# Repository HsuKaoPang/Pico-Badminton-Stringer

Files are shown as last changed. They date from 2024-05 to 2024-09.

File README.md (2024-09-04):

# Pico Stringer
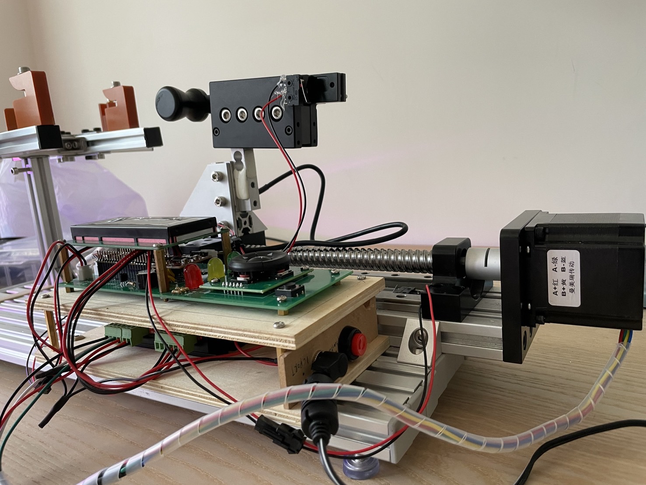
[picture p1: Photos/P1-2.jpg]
images1-1

The project is my version of how to make a badminton stringer, based on [PicoBETH](https://github.com/206cc/PicoBETH) DIY badminton stringer prjoect. 
I published the assemable guildline on [Instructables](https://www.instructables.com/DIY-Electric-Badminton-Stringers/). 

## Modification
Compare to original PicoBETH project, several modifications are listed below. 

### Hardware:
1. Based on a simple badminton stringer, which I bought from [Taobao](https://item.taobao.com/item.htm?_u=t20cga269s9bcb&id=737728917603&spm=a1z09.2.0.0.3fa02e8dvmYHSh). the stringer is made mostly by 2020 and 2060 alumium extrusions.

2. Applying extra 2060 alumium extrusions and alumium extrusion parts as the project's platform.
3. GX-80 1610 double-guided liner guideway with 200mm stroke is adopted.
4. Change Stepper motor driver to DM542C stepper driver.
In my past experience, DM542C could run stepper motor smoother and quieter then TB6600. It also supports more microstep and current adjuestments.

5. Custom-designed PCB board.
6. Intergrated HX711 layout based on [Sparkfun hx711 module](https://www.sparkfun.com/products/13879)

PCB V2.0 Updated:
1. Shrink PCB size to 55.00 x 176.00 mm
2. Extra 12V power pin is preserved for further stepper motor driver development.
3. rearrangement of connector pin.
4. 5-way switch intergrated.
5. polygon poured on both side.

### Software:
[main.py]() is slightly modified to fit DM542C driver.

## Worning

I improved the stringer's strength before I start the project. If your stringer is not robost, I strongly advise against undertaking this project. A weak stringer platform might deform after applying tension, causing the racket frame to deform into round shape or even damage the racket.

## Documents

1. Schmatic diagrams

2. GERBER file
3. BOM of customized pcb board
4. BOM of stringer platfrom hardware
5. Softwares 
## Acknowledgements

 - [PicoBETH](https://github.com/206cc/PicoBETH)
 - [Simple badmintion Stringer](https://item.taobao.com/item.htm?_u=t20cga269s9bcb&id=737728917603&spm=a1z09.2.0.0.3fa02e8dvmYHSh)
 - [Sparkfun HX711](https://www.sparkfun.com/products/13879)
 - [Micropython - hx711-pico-mpy](https://github.com/endail/hx711-pico-mpy)
 - [Micropython - RPI-PICO-I2C-LCD](https://github.com/T-622/RPI-PICO-I2C-LCD)

## Support

For support, feel free to contact me through bill10361239@gmail.com.

## Authors

- [@HsuKaoPang](https://www.github.com/HsuKaoPang)

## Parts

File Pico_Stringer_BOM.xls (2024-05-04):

Comment | Description | Designator | Footprint | LibRef | Quantity
104 | SMD Cap | C1, C3, C5, C6, C8, C10, C11 | 6-0805_M | C | 7
10uF | SMD Cap | C2, C4, C7, C9 | C1210_M | C | 4
IN5819 | Schottky Diode | D1 | DO-41 | D Schottky | 1
LED_G | Typical RED, GREEN, YELLOW, AMBER GaAs LED | D2 | 10mm LED | LED2 | 1
LED_Y | Typical RED, GREEN, YELLOW, AMBER GaAs LED | D3 | 10mm LED | LED2 | 1
LED_R | Typical RED, GREEN, YELLOW, AMBER GaAs LED | D4 | 10mm LED | LED2 | 1
Botton head | 2P Connector | J1 | XH2.54-LI-2P | Header 2 | 1
Front Limit | 2P Connector | J2 | XH2.54-LI-2P | Header 2 | 1
Rear Limit | 2P Connector | J3 | XH2.54-LI-2P | Header 2 | 1
STEPPER | DIR PUL | J4 | XH2.54-LI-4P | Header 4 | 1
Exit Botton | 2P Connector | J5 | 12x12mm SWITCH | Header 2 | 1
5-way switch | 6P Connector | J6 | 5WAY_SWITCH | Header 6 | 1
2004 LCD | 2004 I2C LCD | J7 | HDR1X4 | Header 4 | 1
HX711 | HX711 module | J8 | HX711_MODULE | Header 4 | 1
20KG | Keyes Hx711 module | J9 | HDR1X4 | Header 4 | 1
HDR-1X2 | 5V | JP1 | XH2.54-LI-2P | Header 2 | 1
10uH | SMD Ind | L1 | L 1210 | L | 1
Buzzer | Magnetic Transducer Buzzer | LS1 | Buzzer | Buzzer | 1
SS8050 | NPN | Q1 | TO92A | 8050-DIP | 1
MMBT4403 | PNP | Q2 | SOT23-3L | 8550-SMD | 1
150 | Resistor | R1, R3, R4 | AXIAL-0.3 | Res1 | 3
10K | Resistor | R2 | AXIAL-0.3 | Res1 | 1
1K | Resistor | R5 | AXIAL-0.3 | Res1 | 1
10K | SMD Res | R6 | 6-0805_N | R | 1
20K | SMD Res | R7 | 6-0805_M | R | 1
0K | SMD Res | R8 | 6-0805_M | R | 1
8.2K | SMD Res | R9 | 6-0805_M | R | 1
100 | SMD Res | R10, R11 | 6-0805_M | R | 2
Pi Pico |  | U1 | PICO | Pi Pico | 1
HX711 |  | U2 | SOP16 | HX711 | 1
AMS1117-5.0 | Voltage Regulator | VR1 | AMS1117 | Volt Reg | 1

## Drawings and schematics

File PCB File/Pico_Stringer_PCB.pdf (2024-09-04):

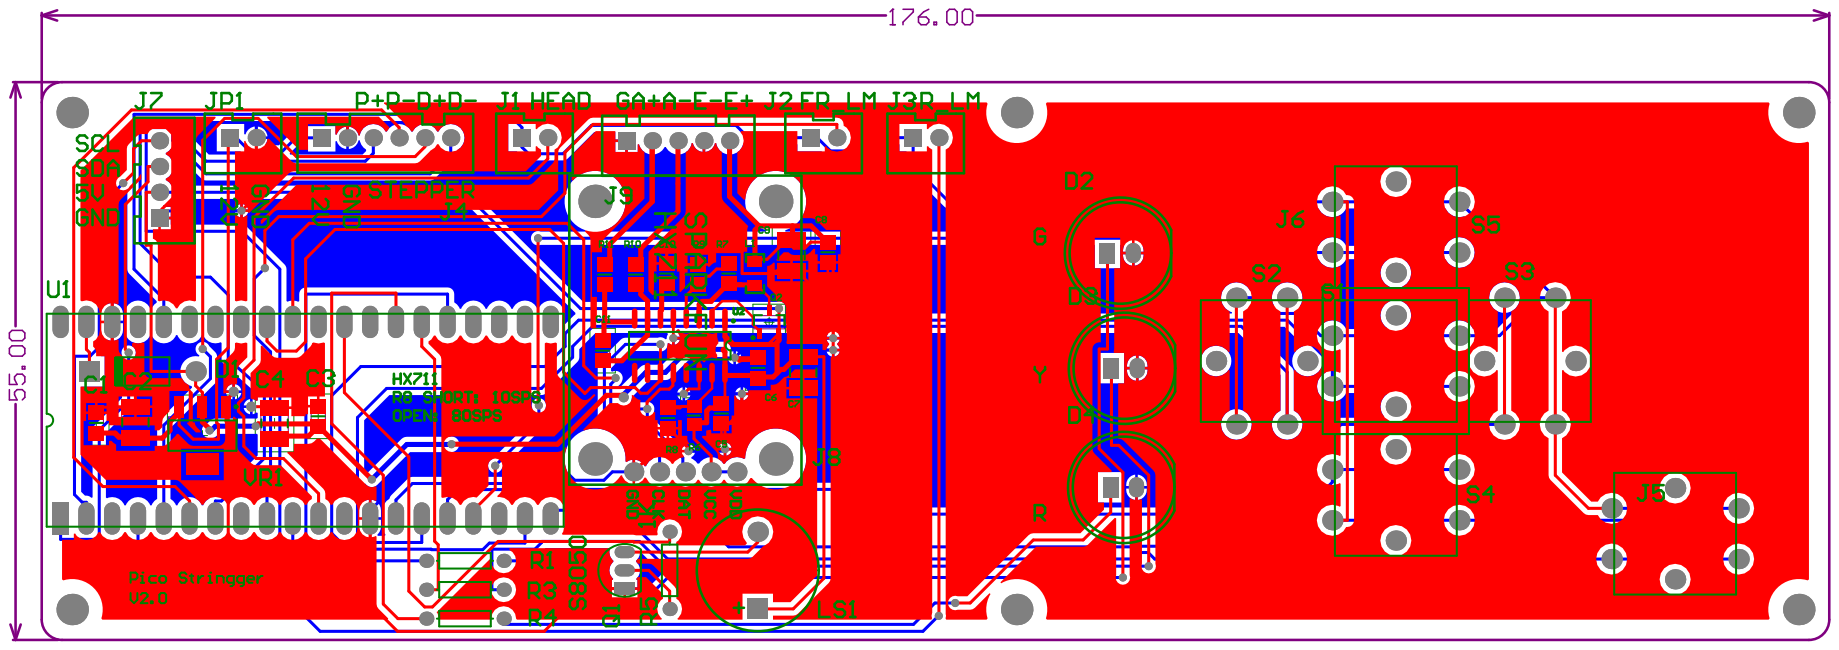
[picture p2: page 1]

Comment | Description | Designator | Footprint | LibRef | Quantity
104 | 贴片电容 | C1 | 6-0805_M | C | 1
10uF | 贴片电容 | C2 | C1210_M | C | 1
104 | 贴片电容 | C3 | 6-0805_M | C | 1
10uF | 贴片电容 | C4 | C1210_M | C | 1
104 | 贴片电容 | C5 | 6-0805_M | C | 1
104 | 贴片电容 | C6 | 6-0805_M | C | 1
10uF | 贴片电容 | C7 | C1210_M | C | 1
104 | 贴片电容 | C8 | 6-0805_M | C | 1
10uF | 贴片电容 | C9 | C1210_M | C | 1
104 | 贴片电容 | C10 | 6-0805_M | C | 1
104 | 贴片电容 | C11 | 6-0805_M | C | 1
IN5819 | Schottky Diode | D1 | DO-41 | D Schottky | 1
LED_G | Typical RED, GREEN, YELLOW, AMBER GaAs LED D2 | | 10mm LED | LED2 | 1
LED_Y | Typical RED, GREEN, YELLOW, AMBER GaAs LED D3 | | 10mm LED | LED2 | 1
LED_R | Typical RED, GREEN, YELLOW, AMBER GaAs LED D4 | | 10mm LED | LED2 | 1
Botton head | 2P接插件 | J1 | XH2.54-LI-2P | Header 2 | 1
Front Limit | 2P接插件 | J2 | XH2.54-LI-2P | Header 2 | 1
Rear Limit | 2P接插件 | J3 | XH2.54-LI-2P | Header 2 | 1
6pin STEPPER | Header, 6-Pin | J4 | XH2.54-LI-6P | Header 6 | 1
Exit Botton | 2P接插件 | J5 | R-Button | Header 2 | 1
5-way switch | | J6 | 5-head button | 5-way switch | 1
2004 LCD | 2004 I2C LCD | J7 | XH2.54-LI-4P | Header 4 | 1
HX711 | SPARKFUN_HX711J8 | | SPARKFUN_HX711Header 5 | | 1
HDR-1X5 | Keyes Hx711 moduleJ9 | | XH2.54-LI-5P | Header 5 | 1
HDR-1X2 | 5V | JP1 | XH2.54-LI-2P | Header 2 | 1
10uH | 小功率贴片电感 | L1 | L 0805 | L | 1
Buzzer | Magnetic Transducer Buzzer LS1 | | Buzzer | Buzzer | 1
SS8050 | 高频放大-NPN型 | Q1 | TO92A | 8050-DIP | 1
MMBT4403 | 高频放大-PNP型 | Q2 | SOT23-3L | 8550-SMD | 1
150 | Resistor | R1 | AXIAL-0.3 | Res1 | 1
150 | Resistor | R3 | AXIAL-0.3 | Res1 | 1
150 | Resistor | R4 | AXIAL-0.3 | Res1 | 1
1K | Resistor | R5 | AXIAL-0.3 | Res1 | 1
10K | 贴片电阻 | R6 | 6-0805_N | R | 1
20K | 贴片电阻 | R7 | 6-0805_M | R | 1
0K | 贴片电阻 | R8 | 6-0805_M | R | 1
8.2K | 贴片电阻 | R9 | 6-0805_M | R | 1
100 | 贴片电阻 | R10 | 6-0805_M | R | 1
100 | 贴片电阻 | R11 | 6-0805_M | R | 1
Pi Pico | | U1 | PICO | Pi Pico | 1
HX711 | | U2 | SOP16 | HX711 | 1
AMS1117-5.0 | Voltage Regulator | VR1 | AMS1117 | Volt Reg | 1

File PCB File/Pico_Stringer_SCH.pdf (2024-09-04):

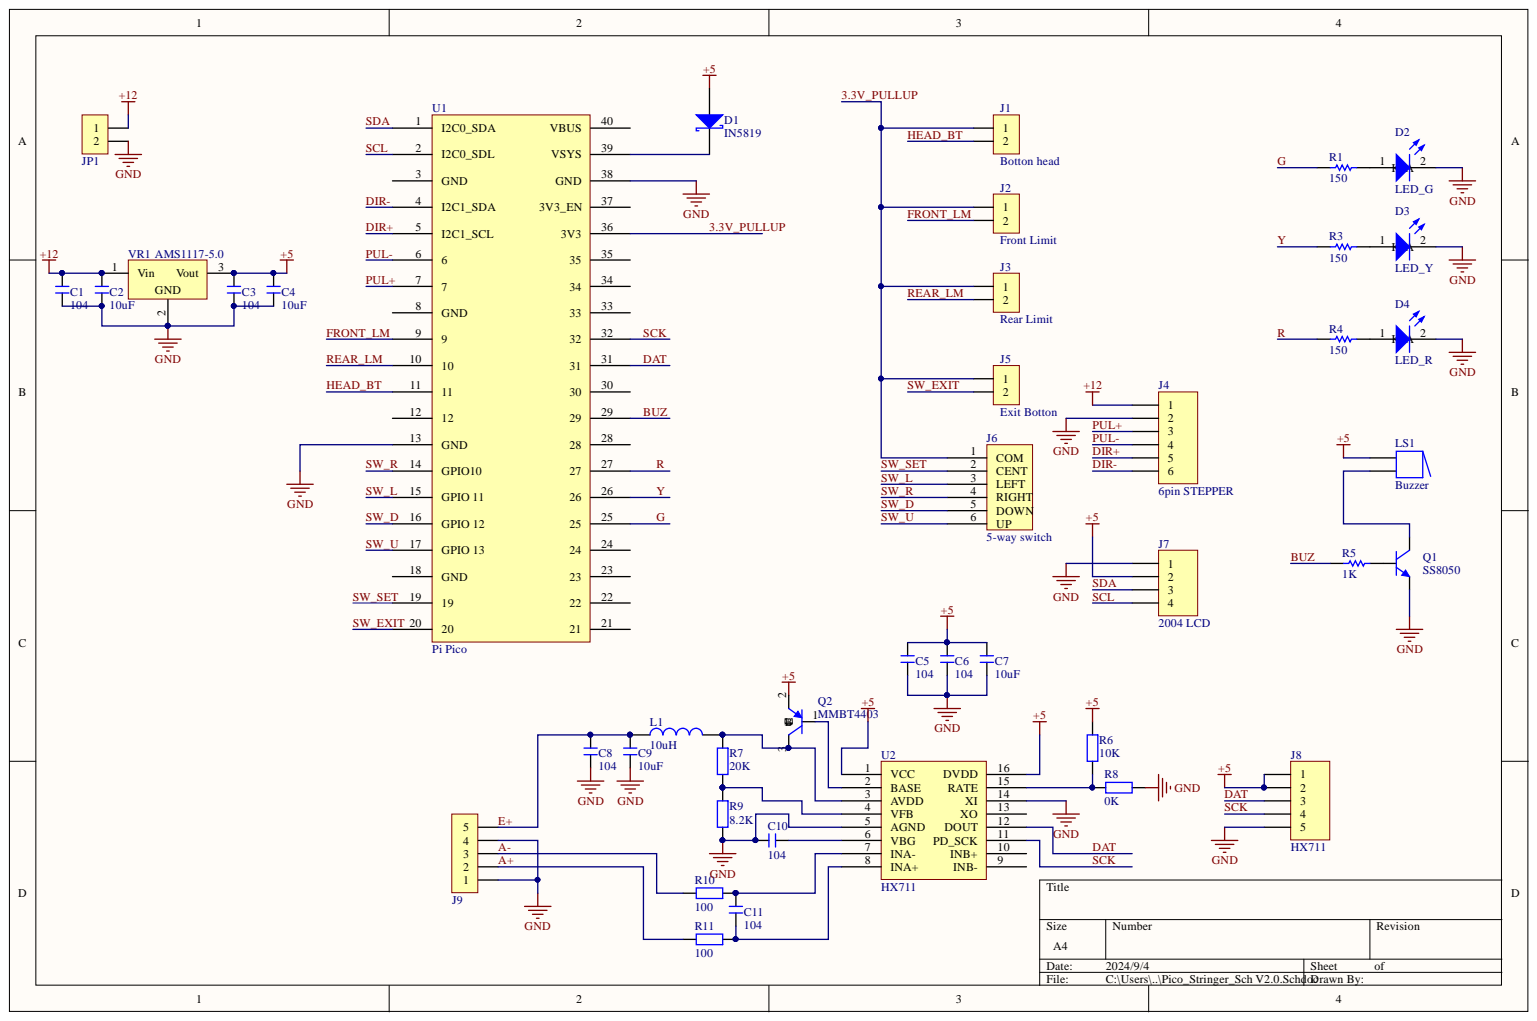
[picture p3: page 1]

A + | G N D 0 | 1 0 4 | SCK

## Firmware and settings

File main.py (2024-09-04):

# MIT License
# 
# Copyright (c) 2023 Kuo Yang-Yang <MAIL: 500119.cpc@gmail.com IG:206cc.tw>
#                                  <WEB: https://github.com/206cc/PicoBETH>
#
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
# GitHub  https://github.com/206cc/PicoBETH
# YouTube https://www.youtube.com/@kuokuo702
# Please go to https://github.com/206cc/PicoBETH?tab=readme-ov-file#final-settings for instructions on how to configure FT and HX parameters.
# Basic parameters (settings saved in CFG_NAME will take precedence if there are stored parameter values)
# 第一次開機請至 https://github.com/206cc/PicoBETH?tab=readme-ov-file#final-settings 觀看如何設定 FT、HX 參數
# 基本參數(如 CFG_NAME 內有儲存參數值會以的存檔的設定為主)
FIRST_TEST = 1       # Self-test check on first boot
                     # 第一次開機自我測試檢查
HX711_CAL = 20.00    # Calibration coefficients for HX711 load cell amplifier
                     # HX711張力放大器校正系數
CORR_COEF_AUTO = 1   # Self-learning tension parameter 0=off 1=on
                     # 自我學習張力參數 0=off 1=on
LB_KG_SELECT = 0     # Setting for pounds or kilograms, 0=both can be set, 1=only pounds, 2=only kilograms
                     # 磅或公斤的設定，0=皆可設定，1=只設定磅，2=只設定公斤
DEFAULT_LB = 20.0    # Default weight in LB
                     # 預設磅數
PRE_STRECH = 10      # Default Pre-Strech
                     # 預設預拉
KNOT = 15            # Default Knot
                     # 預設打結
LB_MAX = 35.0        # Maximum tension in LB
                     # 設定張緊的最高磅數
LB_MIN = 15.0        # Minimum tension in LB
                     # 設定張緊的最低磅數
PS_MAX = 30          # Maximum percentage in Pre-Strech
                     # 設定預拉的最高%數
KNOT_MIN = 5         # Minimum percentage for knot
                     # 打結增最低%數
KNOT_MAX = 30        # Maximum percentage for knot
                     # 打結增最高%數
HX711_MAX = 25.00    # Maximum value for HX711 calibration parameter
                     # HX711校正參數最大值
HX711_MIN = 15.00    # Minimum value for HX711 calibration parameter
                     # HX711校正參數最小值
FT_ADD_MAX = 4       # Maximum value for Constant-pull adjustment parameter
                     # 恆拉微調參數最大值
FT_ADD_MIN = 1       # Minimum value for Constant-pull adjustment parameter
                     # 恆拉微調參數最小值
FT_ADD = 1           # Number of steps for stepper motor during constant-pull adjustment
                     # 恆拉微調時步進馬達的步數
CP_SW = 1            # Constant-pull switch 0=off, 1=on
                     # 恆拉開關 0=關閉，1=啟用
CP_SLOW = 30         # Gram value for triggering constant tension adjustment
                     # 觸發恆拉微調公克值
CP_FAST = 40         # Gram value for triggering the fast constant-pull mechanism
                     # 觸發快速恆拉微調公克值
BZ_SW = 1            # Buzzer switch 0=off, 1=on
                     # 蜂鳴器開關 0=關閉，1=啟用
ABORT_GRAM = 20000   # Maximum abort grams (about 44 lb)
                     # 最大中斷公克(約44磅)
LOG_MAX = 50         # Maximum LOG retention records (Please do not set too large to avoid memory exhaustion and inability to boot)
                     # 最大LOG保留記錄(請勿太大，以免記憶體耗盡無法開機)
CA_REM = 0.1         # LB value for HX711 Tension calibration reminder
                     # 張力校正提醒(磅)
HX711_DIFRT = 1.0    # Check the HX711 difrt in grams.
                     # 檢查HX711飄移值(公克)
                    
import time, _thread, machine, os
from machine import I2C, Pin
from src.hx711 import hx711          # from https://github.com/endail/hx711-pico-mpy
from src.pico_i2c_lcd import I2cLcd  # from https://github.com/T-622/RPI-PICO-I2C-LCD

# Other parameters 其它參數
VERSION = "2.32Bill_rev"
VER_DATE = "2024-08-15"
SAVE_CFG_ARRAY = ['DEFAULT_LB','PRE_STRECH','CORR_COEF','MOTO_STEPS','HX711_CAL','TENSION_COUNT','BOOT_COUNT', 'LB_KG_SELECT','CP_SW','FT_ADD','CORR_COEF_AUTO','KNOT','MOTO_MAX_STEPS','FIRST_TEST','BZ_SW','HX711_V0'] # Saved variables 存檔變數
MENU_ARR = [[4,0],[4,1],[4,2],[14,0],[15,0],[14,1],[15,1],[17,1],[18,1],[19,1],[11,3],[19,3]] # Array for LB setting menu 設定選單陣列
UNIT_ARR = ['LB&KG', 'LB', 'KG']
ONOFF_ARR = ['Off', 'On ']
MA_ARR = ['M', 'A']
ML_ARR = ['N', 'L']
PSKT_ARR = ['PS', 'KT']
TS_LB_ARR = [[4,0],[5,0],[7,0]] # Array for LB setting 磅調整陣列
TS_KG_ARR = [[4,1],[5,1],[7,1]] # Array for KG setting 公斤調整陣列
TS_KT     = [[14,0]]            # Switching between knot and Pre-Strech 打結鍵切換
TS_PS_ARR = [[17,0],[18,0]]     # Array for Pre-Strech 預拉調整陣列
MOTO_FORW_W = [[0, 1, 1, 0],[0, 1, 1, 0],[1, 0, 1, 0],[1, 0, 1, 0]] # 步進馬達正轉參數
MOTO_BACK_W = [[0, 1, 0, 1],[0, 1, 0, 1],[1, 0, 0, 1],[1, 0, 0, 1]] # 步進馬達反轉參數
MOTO_MAX_STEPS = 1000000
MOTO_RS_STEPS = 2000    # Number of steps to retreat during slider reset 滑台復位時退回的步數
MOTO_SPEED_V1 = 0.0001  # Stepper motor high speed 步進馬達高速
MOTO_SPEED_V2 = 0.001   # Stepper motor low speed 步進馬達低速
BUTTON_SLEEP = 0.1      # Button waiting time in seconds 按鍵等待秒數
CORR_COEF = 1.00        # Tension coefficient 張力系數
PRE_STEP = 30
HX711_V0 = 0
CONFIG_FILE = 'config.cfg'
LOG_FILE = 'logs.txt'

# Stepper motor 步進馬達
IN1 = machine.Pin(4, machine.Pin.OUT) # PUL-
IN2 = machine.Pin(5, machine.Pin.OUT) # PUL+
IN3 = machine.Pin(2, machine.Pin.OUT) # DIR-
IN4 = machine.Pin(3, machine.Pin.OUT) # DIR+

# Limit switches for slider front and rear limits 滑台限位前後限位感應開關
MOTO_SW_FRONT = Pin(6, Pin.IN, Pin.PULL_DOWN)  # Front limit 滑軌前限位感應開關
MOTO_SW_REAR = Pin(7, Pin.IN, Pin.PULL_DOWN)   # Rear limit 滑軌後限位感應開關

# Function keys 功能按鍵
BUTTON_HEAD = Pin(8, Pin.IN, Pin.PULL_DOWN)     # Bead clamp head activation button 珠夾頭啟動按鍵
BUTTON_UP = Pin(13, Pin.IN, Pin.PULL_DOWN)      # Up button 上按鍵
BUTTON_DOWN = Pin(12, Pin.IN, Pin.PULL_DOWN)    # Down button 下按鍵
BUTTON_LEFT = Pin(11, Pin.IN, Pin.PULL_DOWN)    # Left button 左按鍵
BUTTON_RIGHT = Pin(10, Pin.IN, Pin.PULL_DOWN)   # Right button 右按鍵
BUTTON_SETTING = Pin(14, Pin.IN, Pin.PULL_DOWN) # Setting button 設定按鍵
BUTTON_EXIT = Pin(15, Pin.IN, Pin.PULL_DOWN)    # Exit button 取消按鍵
BUTTON_LIST = {"BUTTON_HEAD":0,
               "BUTTON_SETTING":0,
               "BUTTON_EXIT":0,
               "BUTTON_UP":0,
               "BUTTON_DOWN":0,
               "BUTTON_LEFT":0,
               "BUTTON_RIGHT":0}                # Button list 按鈕列表
BUTTON_CLICK_MS = 500                           # Button click milliseconds 按鈕點擊毫秒

# LED
LED_GREEN = Pin(19, machine.Pin.OUT)  # Green 綠
LED_YELLOW = Pin(20, machine.Pin.OUT) # Yellow 黃
LED_RED = Pin(21, machine.Pin.OUT)    # Red 紅

# Active buzzer 蜂鳴器
BEEP = Pin(22, machine.Pin.OUT)

# Global variables 全域變數
LB_CONV_G = 0
TENSION_MON = 0
MOTO_MOVE = 0
MOTO_WAIT = 0
MOTO_STEPS = 0
CURSOR_XY_TMP = 0
CURSOR_XY_TS_TMP = 1
HX711 = {"RATE":0, "DIFF":0, "V0":[], "CP_HZ":0.125, "HX711_CAL": 20.00}
TENSION_COUNT = 0
BOOT_COUNT = 0
TIMER = 0
ERR_MSG = ""
ABORT_LM = 0
TS_ARR = []
LOGS = []
TENSION_MON_TEMP = 0
KNOT_FLAG = 0

# 2004 i2c LCD
I2C_ADDR     = 0x27
I2C_NUM_COLS = 20
i2c = I2C(0, sda=machine.Pin(0), scl=machine.Pin(1), freq=400000)
lcd = I2cLcd(i2c, I2C_ADDR, 4, I2C_NUM_COLS)

# HX711
hx = hx711(Pin(27), Pin(26))
hx.set_power(hx711.power.pwr_up)
hx.set_gain(hx711.gain.gain_128)
hx.set_power(hx711.power.pwr_down)
hx711.wait_power_down()
hx.set_power(hx711.power.pwr_up)
hx711.wait_settle(hx711.rate.rate_80)

# Read file parameters 參數讀取
def config_read():
    global HX711
    try:
        file = open(CONFIG_FILE, "r")
        data = file.read()
        config_list = data.split(",")
        for val in config_list:
            cfg = val.split("=")
            if cfg[0]:
                if "." in cfg[1]:
                    globals()[cfg[0]] = float(cfg[1])
                else:
                    globals()[cfg[0]] = int(cfg[1])
                    
        file.close()
        HX711['HX711_CAL'] = HX711_CAL
    except OSError:  # failed
       pass

# Writing file Parameter 參數寫入
def config_save(flag):
    global HX711_CAL, HX711
    try:
        if flag == 1:
            HX711['HX711_CAL'] = HX711_CAL
            
        elif flag == 0:
            tmp_HX711_CAL = HX711_CAL
            HX711_CAL = HX711['HX711_CAL']
        
        file = open(CONFIG_FILE, "w")
        save_cfg = ""
        for val in SAVE_CFG_ARRAY:
            if isinstance(globals()[val], int) or isinstance(globals()[val], float):
                save_cfg = save_cfg + val +"=" + str(globals()[val]) + ","

        file.write(save_cfg)
        file.close()
        if flag == 0:
            HX711_CAL = tmp_HX711_CAL
    except OSError:  # failed
       pass

# Writing file LOG 寫入LOG
def logs_save(log_str, flag):
    try:
        file = open(LOG_FILE, flag)
        for element in reversed(log_str):
            save_log = ""
            for val in element:
                save_log = save_log + str(val) + ","

            file.write(save_log[:-1] + "\n") 
        file.close()
    except OSError:  # failed
       pass

# Read file LOG 讀取LOG
def logs_read():
    global LOGS
    try:
        fp = open(LOG_FILE, "r")
        line = fp.readline()
        while line:
            log_list = line.strip().split(",")
            LOGS.insert(0, log_list)
            line = fp.readline()
            if len(LOGS) > LOG_MAX:
                LOGS = LOGS[:LOG_MAX]
        
        fp.close()
        logs_save(LOGS, "w")
    except OSError:  # failed
       pass

# Active buzzer 有源蜂鳴器
def beepbeep(run_time):
    if BZ_SW == 1:
        BEEP.on()
        time.sleep(run_time)
        BEEP.off()
    else:
        time.sleep(run_time)

# Tension display 張力顯示
def tension_info(tension):
    if tension is None:
        tension = TENSION_MON
    
    show_lcd("{: >4.1f}".format(tension * 0.0022), 9, 0, 4)
    show_lcd("{: >4.1f}".format(tension / 1000), 9, 1, 4)
    show_lcd("{: >5d}G".format(tension), 14, 3, 6)
    return tension

# Stepper motor operation 步進馬達作動
def setStep(in_w):
    IN1.value(in_w[0])
    IN2.value(in_w[1])
    IN3.value(in_w[2])
    IN4.value(in_w[3])

# Increase in tension 張力增加
def forward(delay, steps, check, init):
    global MOTO_MOVE, MOTO_WAIT
    LED_GREEN.off()
    MOTO_MOVE = 1
    for i in range(0, steps):
        if check == 1:
            if MOTO_WAIT == 1:
                MOTO_MOVE = 0
                MOTO_WAIT = 0
                return(0)
            
            
            # Exit button 離開按鍵
            if button_list('BUTTON_EXIT'):
                moto_goto_standby()
                MOTO_MOVE = 0
                MOTO_WAIT = 0
                return("Abort")
            
            # Tension sensor anomaly or no string (tension less than 5 lb after ABORT_LM) 張力傳感器異常、無夾線(行程已過ABORT_LM時張力小於5磅)
            if i > ABORT_LM and TENSION_MON < 2267:
                moto_goto_standby()
                MOTO_MOVE = 0
                MOTO_WAIT = 0
                return("No String?")
        
        # Exceeding the rear limit switch 超過後限位SW
        if MOTO_SW_REAR.value():
            moto_goto_standby()
            if init:
                return i
                
            MOTO_MOVE = 0
            MOTO_WAIT = 0
            return("Over Limits")
        
        # Exceeding the maximum specified tension 超過最大指定張力
        if ABORT_GRAM < TENSION_MON:
            moto_goto_standby()
            MOTO_MOVE = 0
            MOTO_WAIT = 0
            return("ABORT GRAM")
        
        setStep(MOTO_FORW_W[0])
        setStep(MOTO_FORW_W[1])
        setStep(MOTO_FORW_W[2])
        setStep(MOTO_FORW_W[3])
        
        if(i < PRE_STEP):
            time.sleep(MOTO_SPEED_V2)
        else:
            time.sleep(delay)
        

# Tension decrease 張力減少
def backward(delay, steps, check, init):
    global MOTO_STEPS
    LED_GREEN.off()
    for i in range(0, steps):
        if check == 1:
            if MOTO_SW_FRONT.value():
                if init == 1:
                    MOTO_STEPS = i
                    
                time.sleep(0.1)
                forward(MOTO_SPEED_V1, MOTO_RS_STEPS, 0, 0)
                return 0 
            
        setStep(MOTO_BACK_W[0])
        setStep(MOTO_BACK_W[1])
        setStep(MOTO_BACK_W[2])
        setStep(MOTO_BACK_W[3])
        
        if(i < PRE_STEP):
            time.sleep(MOTO_SPEED_V2)
        else:
            time.sleep(delay)

# Slider reset 滑台復位
def moto_goto_standby():
    LED_YELLOW.on()
    time.sleep(0.3)
    backward(MOTO_SPEED_V1, MOTO_MAX_STEPS, 1, 0)
    beepbeep(0.3)
    LED_YELLOW.off()
    LED_GREEN.on()

# LCD display
def show_lcd(text, x, y, length):
    text = text[:length]
    text = f'{text :{" "}<{length}}'
    lcd.move_to(x, y)
    lcd.putstr(text)

# Button detection 按鈕偵測
def button_list(key):
    global BUTTON_LIST
    if BUTTON_LIST[key]:
        BUTTON_LIST[key] = 0
        return True
    else:
        return False
    
# Second core 第二核心
def tension_monitoring():
    global TENSION_MON, MOTO_WAIT, HX711, BUTTON_LIST, TENSION_MON_TEMP
    # HX711 zeroing 歸零HX711
    v0_arr = []
    t0 = time.ticks_ms()
    while True:
        if val := hx.get_value_noblock():
            HX711["V0"].append(val)
            if (time.ticks_ms() - t0) > 1000:
                v0_arr = sorted(HX711["V0"])
                v0 = v0_arr[int((len(v0_arr)/2))]
                HX711["HX711_V0"] = v0
                HX711["DIFF"] = v0_arr[-1] - v0_arr[0]
                HX711["RATE"] = len(v0_arr)
                HX711["CP_HZ"] = round(1 / HX711["RATE"], 3)
                break
    
    while True:
        # Tension monitoring 張力監控
        if val := hx.get_value_noblock():
            TENSION_MON = int((val-(v0))/100*(HX711_CAL/20))
            if MOTO_MOVE == 1:
                if LB_CONV_G < (TENSION_MON * CORR_COEF):
                    TENSION_MON_TEMP = TENSION_MON
                    MOTO_WAIT = 1
        
        # Button detection 按鍵偵測
        for key in BUTTON_LIST:
            if globals()[key].value() == 1:
                BUTTON_LIST[key] = time.ticks_ms()
            elif BUTTON_LIST[key]:
                if (time.ticks_ms() - BUTTON_LIST[key]) > BUTTON_CLICK_MS:
                    BUTTON_LIST[key] = 0

def lb_kg_select():
    global TS_ARR
    if LB_KG_SELECT == 1:
        TS_ARR = TS_LB_ARR + TS_KT + TS_PS_ARR
    elif LB_KG_SELECT == 2:
        TS_ARR = TS_KG_ARR + TS_KT + TS_PS_ARR
    else:
        TS_ARR = TS_LB_ARR + TS_KG_ARR + TS_KT + TS_PS_ARR

# Boot initialization 開機初始化
def init():
    global LB_CONV_G, TS_ARR, ERR_MSG, ABORT_LM, MOTO_RS_STEPS, MOTO_MAX_STEPS, BOOT_COUNT, ABORT_GRAM, FT_ADD, BZ_SW
    max_MOTO_MAX_STEPS = MOTO_MAX_STEPS
    config_read()
    bz_sw_tmp = BZ_SW
    BZ_SW = 1
    lb_kg_select()
    show_lcd(" **** PicoBETH **** ", 0, 0, I2C_NUM_COLS)
    show_lcd("Version: " + VERSION, 0, 1, I2C_NUM_COLS)
    show_lcd("Date: " + VER_DATE, 0, 2, I2C_NUM_COLS)
    show_lcd("Ghub: 206cc/PicoBETH", 0, 3, I2C_NUM_COLS)
    time.sleep(3)
    LED_RED.on()
    main_interface()
    ori_ABORT_GRAM = ABORT_GRAM
    ABORT_GRAM = 1000
    LB_CONV_G = min(int((DEFAULT_LB * 453.59237) * ((PRE_STRECH + 100) / 100)), int(LB_MAX * 453.59237))
    show_lcd("Tension monitoring...", 0, 2, I2C_NUM_COLS)
    _thread.start_new_thread(tension_monitoring, ())
    
    # Waiting for HX711 zeroing 等待 HX711 歸零
    i = 0
    while True:
        if HX711["RATE"] != 0:
            break
        
        if i > 20:
            ERR_MSG = "ERR: HX711@Zero #1"
            break
        
        i = i + 1
        time.sleep(0.1)
        
    # Sampling error less than 0.01 grams (HX711 damaged?) 取樣誤差過小於 0.01公克(HX711損壞?)
    if HX711["DIFF"] < 10:
        ERR_MSG = "ERR: HX711@Zero #2"
        
    # Sampling value too small (HX711 damaged?) 取樣值過小(HX711損壞?)
    if HX711["V0"][0] < 0:
        ERR_MSG = "ERR: HX711@Zero #3"

    # Check if HX711 RATE exceeds 75Hz 檢查 HX711 RATE 是否超過 75Hz
    if HX711["RATE"] < 75:
        ERR_MSG = "ERR: HX711@"+ str(HX711["RATE"]) +"Hz"

    # Sampling error exceeds HX711_DIFRT gram or is less than 0.3G. (unstable) 取樣誤差過大超過 HX711_DIFRT 或小於 0.3公克(不穩定)
    if HX711["DIFF"] > (HX711_DIFRT * 1000) or HX711["DIFF"] < 300:
        ERR_MSG = "ERR: HX_DIFRT@"+ str(round(HX711["DIFF"]/1000,1)) +"G"

    # Standby error exceeds 5 grams (unstable) 待機誤差過大超過 5公克(不穩定)
    if abs(TENSION_MON) > 5:
        ERR_MSG = "ERR: HX711@"+ str(abs(TENSION_MON)) +"G #2"
    
    if ERR_MSG == "":
        if button_list('BUTTON_EXIT'):
            beepbeep(0.5)
            show_lcd("Factory Reset?", 0, 2, I2C_NUM_COLS)
            show_lcd("[UP=Y DOWN=N]", 0, 3, I2C_NUM_COLS)
            while True:
                if button_list('BUTTON_UP'):
                    if CONFIG_FILE in os.listdir():
                        os.rename(CONFIG_FILE, CONFIG_FILE+'.bak')
                    
                    if LOG_FILE in os.listdir():
                        os.remove(LOG_FILE)
                    
                    machine.reset()
                elif button_list('BUTTON_DOWN'):
                    main_interface()
                    break
        elif button_list('BUTTON_SETTING'):
            beepbeep(0.5)
            first_test(1, bz_sw_tmp)
        
        if FIRST_TEST == 1:
            first_test(0, bz_sw_tmp)
        
        logs_read()
        moto_goto_standby()
        show_lcd("Checking motor...", 0, 2, I2C_NUM_COLS)
        ori_MOTO_MAX_STEPS = MOTO_MAX_STEPS
        MOTO_MAX_STEPS = max_MOTO_MAX_STEPS
        MOTO_MAX_STEPS = forward(MOTO_SPEED_V1, MOTO_MAX_STEPS, 0, 1)
        BZ_SW = bz_sw_tmp
        if MOTO_MAX_STEPS == "ABORT GRAM":
            ERR_MSG = "ERR: Abort Gram"
        else:
            MOTO_RS_STEPS = int(int(MOTO_MAX_STEPS) / 20)
            ABORT_LM = int(int(MOTO_MAX_STEPS) * 0.3)
            ABORT_GRAM = ori_ABORT_GRAM
            tmp_FT_ADD = round(FT_ADD * MOTO_MAX_STEPS / ori_MOTO_MAX_STEPS)
            if tmp_FT_ADD != 0:
                FT_ADD = tmp_FT_ADD
            
            moto_goto_standby()
            LED_RED.off()
            if abs(HX711_V0 - HX711["HX711_V0"]) > (CA_REM * 15000):
                show_lcd("HX Need Calibration!", 0, 2, I2C_NUM_COLS)
            else:
                show_lcd("Ready", 0, 2, I2C_NUM_COLS)
                
            beepbeep(0.3)
            BOOT_COUNT = BOOT_COUNT + 1
            config_save(0)
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

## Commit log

2024-04-29 Add files via upload
    Schematic and PCB Layout pdf is uploaded
2024-04-29 Add files via upload
    GERBER Files and NcDrill Files are added.
    [Pico_Stringer_PCB.GBL, Pico_Stringer_PCB.GBS, Pico_Stringer_PCB.GM1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]
2024-05-04 Add files via upload
    PCB BOM file uploaded
    [Pico_Stringer_BOM.xls]
2024-05-09 Add files via upload
    Altium SCH and PCB File Uploaded
    [Pico_Stringer_PCB.PcbDoc, Pico_Stringer_Sch.Schdoc]
2024-05-18 Add files via upload
    better hx711 pcb layout design
    [Pico_Stringer_PCB.PcbDoc]
2024-05-18 Add files via upload
    Better HX711 PCB layout updated
    [Pico_Stringer_PCB.GBL, Pico_Stringer_PCB.GBS, Pico_Stringer_PCB.GTL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]
2024-05-18 Add files via upload
    Assemble photos uploaded
2024-05-18 Add files via upload
    Latest Sch and PCB Updated. HX711 surrounding layout changed. solid copper connected to GND added.
2024-05-19 Add files via upload
    Assemble Photos re-uploaded with orders
2024-05-19 Add files via upload
    design check error fixed. Spaces between 5V and 3mm hole is large enough
2024-09-04 Add files via upload
    Few Updates:
    1. Auto-pull function upgraded.
    2. Up and Down button beep sound cancelled for faster tension setup.
2024-09-04 Delete Pico_Stringer_PCB.PcbDoc
    Remove PCB Files to new folder
    [Pico_Stringer_PCB.PcbDoc]
2024-09-04 Delete Pico_Stringer_PCB.pdf
    Move PCB Files to new Folders
2024-09-04 Delete Pico_Stringer_Sch.Schdoc
    Move PCB Files to new folder
    [Pico_Stringer_Sch.Schdoc]
2024-09-04 Delete Pico_Stringer_Sch.pdf
    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
2024-09-04 Add files via upload
    Pico Stringer V2.0 Uploaded.
    1. Size Changed to 176mmx55mm
    2. 5-way button intergrated.
    3. Extra 12V power pin preserved for further Stepper motor driver development
    4. Layout optimized.
2024-09-04 Rename Project Outputs for Pico Stringer V2.0.rar to Pico Stringer GERBER+NCDrill.rar
    GERBER RAR file name changed
2024-09-04 Delete GERBER File directory
    Remove GERBER File and transfered to New Folder
    [Pico_Stringer_PCB.GBL, Pico_Stringer_PCB.GBS, Pico_Stringer_PCB.GM1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]
2024-09-04 Update README.md
    Pico Stringer PCB V2.0 description upgraded.
